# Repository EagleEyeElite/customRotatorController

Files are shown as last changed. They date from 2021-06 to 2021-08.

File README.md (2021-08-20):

# Satellite Receiver

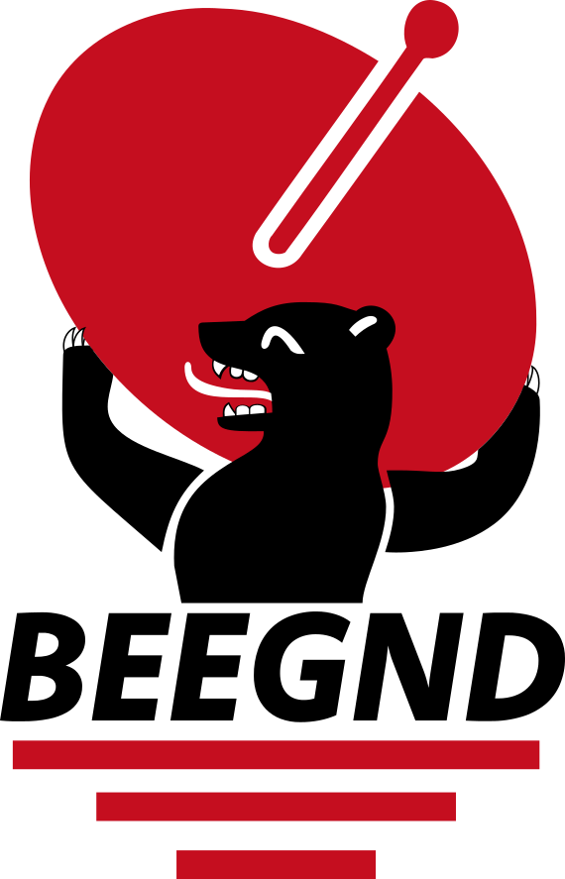
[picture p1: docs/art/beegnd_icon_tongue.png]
BEEGND IMG


Student project: custom rotor design for portable ground station. \
Members of this group:
- Conrad Klaus (code and electronics)
- Prabhpreet S. Data (mechanics, prototype)
- Nasser Mazraani (final design build)

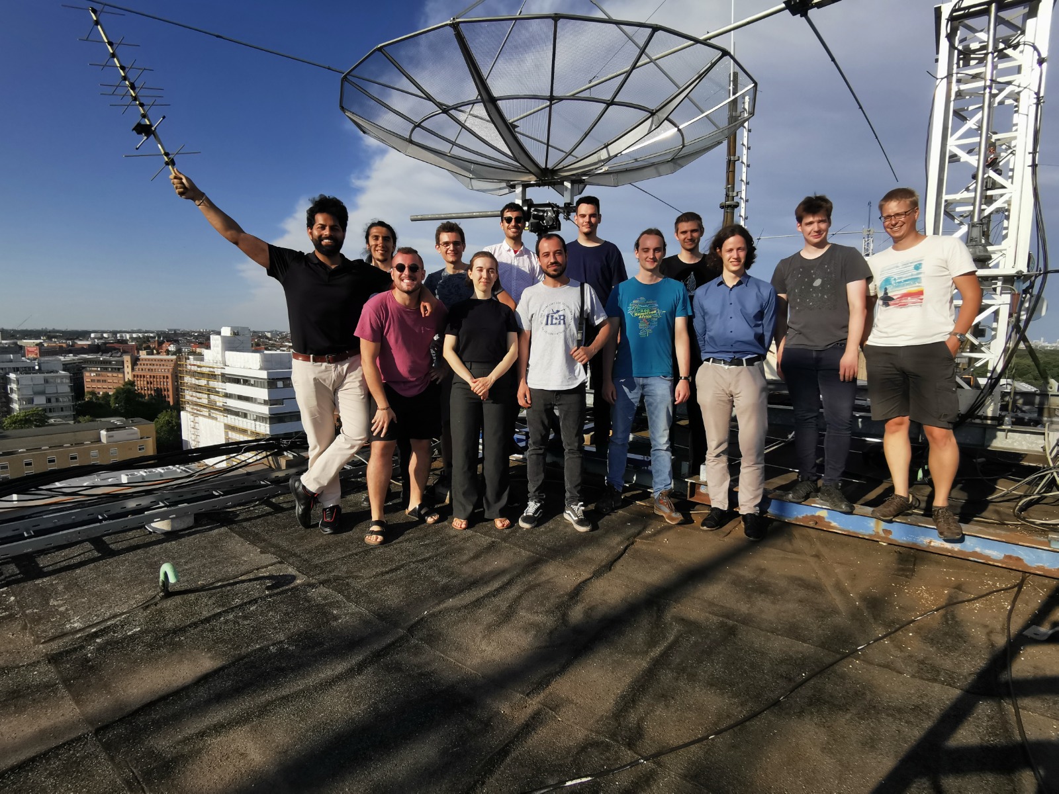
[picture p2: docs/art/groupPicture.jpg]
Satcom Group img
\
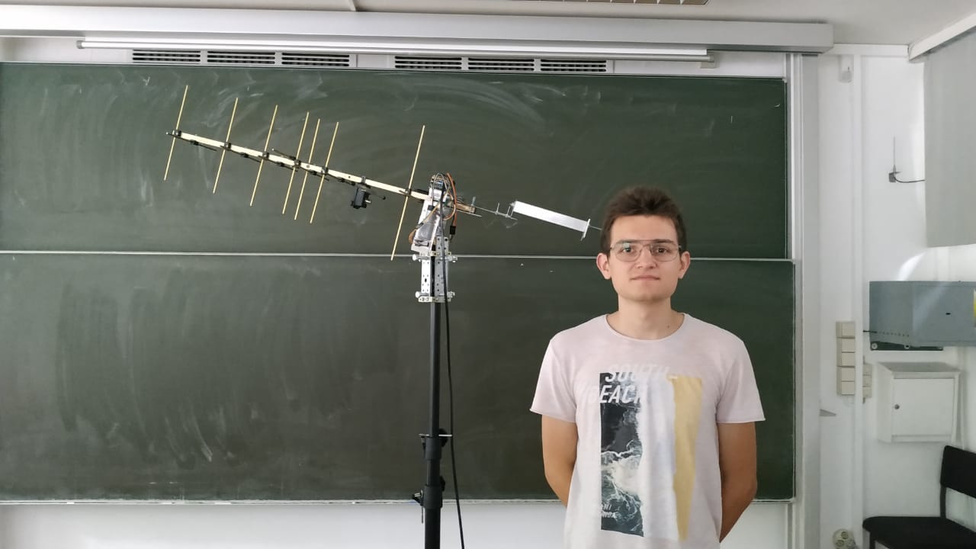
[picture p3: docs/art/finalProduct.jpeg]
Satellite Receiver img


## PCB design
The pcb is designed as a raspberry pi hat to drive the motors and sensors.\
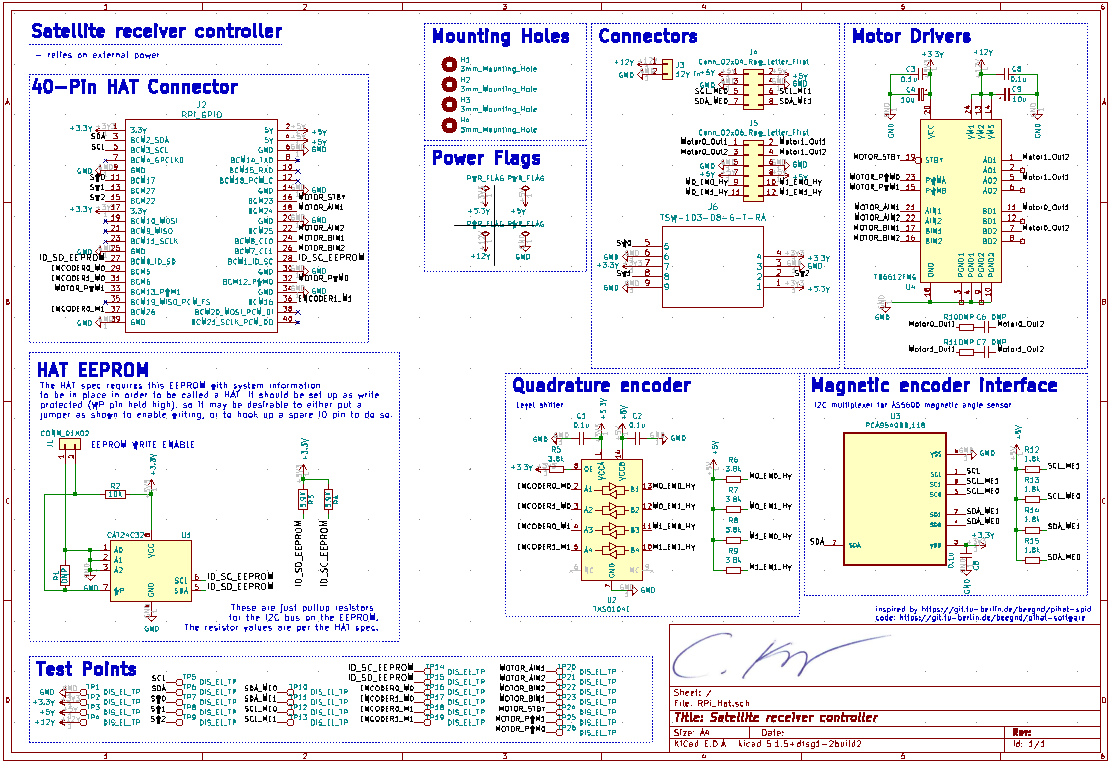
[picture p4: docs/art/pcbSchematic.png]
Pcb Schematic
\
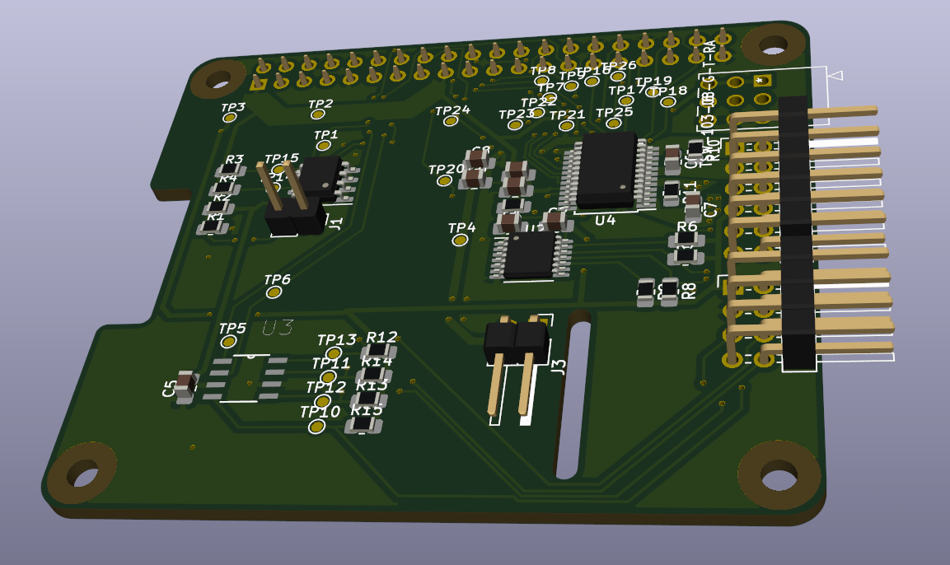
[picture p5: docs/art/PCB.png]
Pcb Image


## Code
Main features:
- Rotctl
- Multithreading
- Sensors: magnetic encoder, quadrature
encoder, switches
- Separate driver modules: h-bridge, i2c
multiplexer etc.
- Position monitoring

For further information: ./src/README.md or ./documentation

Code structure: \
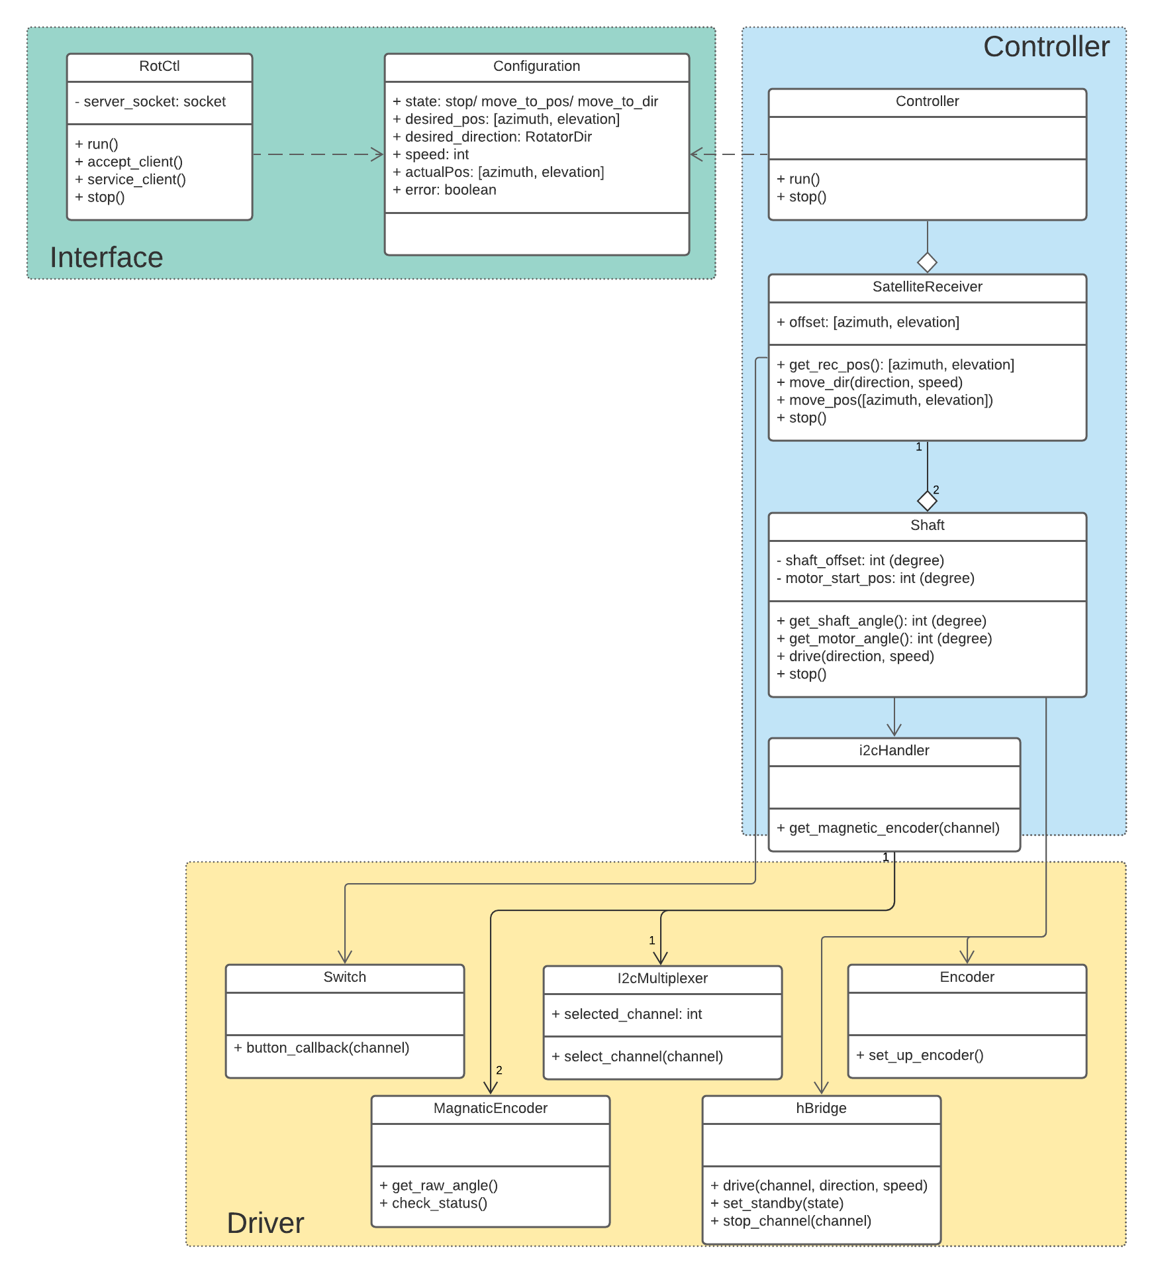
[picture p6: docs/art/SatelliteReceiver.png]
Code structure


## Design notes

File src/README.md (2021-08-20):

# Satellite receiver
Example raspberry pi ip: 10.42.0.101

## Connect to RotCtl API
The satellite receiver is controlled by rotctl. \
Run in terminal to connect to service:
```
rotctl -m 2 -r 10.42.0.101:4533
```

## Start RotCtl service
Start RotCtl service and set up virtual python environment (if needed).
```
python3 -m venv ./venv      # create venv (optional)
source ./venv/bin/activate
python3 -m pip install -r requirements.txt   # install dependencies (optional)
cd satelliteReceiver/src/
./main.py     # start controller
deactivate
```

You may need to enable I2C once in the
[raspberry pi config](https://www.raspberrypi-spy.co.uk/2014/11/enabling-the-i2c-interface-on-the-raspberry-pi).

## Connect to the pi manually
Connect ethernet adapter and raspberry first. \
Run in terminal:
```
$ ifconfig  # copy inet: (usually 10.42.0.1)
$ nmap -n -sP 10.42.0.255/24  # scans the network
```
Copy the ip address from the pi to connect to it via ssh.

Access pi via explorer:
```
nfs://10.42.0.101/home/pi/satcom/customRotatorController
```

## Headless raspberry pi setup
- pc client fstab example (static ip):
  ```  
  10.42.0.101:/home/pi/satcom/customRotatorController /home/conrad/Documents/piGitMnt nfs defaults 0 0
  ```
- [ssh](https://linuxize.com/post/how-to-enable-ssh-on-raspberry-pi/)
- [wifi](https://www.raspberrypi.org/documentation/configuration/wireless/headless.md)
- laptop ethernet setup:
    - [static ip](https://www.circuitbasics.com/how-to-connect-to-a-raspberry-pi-directly-with-an-ethernet-cable/)
    - [dynamic ip](https://stackoverflow.com/questions/16040128/hook-up-raspberry-pi-via-ethernet-to-laptop-without-router)
- [nfs workflow](https://pimylifeup.com/raspberry-pi-nfs/)

## Used hardware
- [Power over ethernet hat](https://www.amazon.de/dp/B091YZ2QSM)
- [Motor 10RPM](https://www.banggood.com/Machifit-JGY-370-DC-12V-103090150RPM-Motor-Reduction-Gear-Turbine-Worm-Self-locking-Encoder-Signal-Feedback-Motor-p-1504101.html)
- [Magnetic encoder](https://www.amazon.de/dp/B08K2Q96V1/)
  
## Sources
- [KiCad pi Hat template](https://github.com/xesscorp/RPi_Hat_Template)

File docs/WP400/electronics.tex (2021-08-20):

\subsection{Electronics}
The custom rotator is controlled by a Raspberry Pi, extended by a custom Raspberry Pi hat. The hat provides functionality to read the safety switches, communicate to two independent magnetic encoders, drive both motors, and monitor the motors speed with a quadrature encoder. The Hat also features an EEPROM, which is specified by the Raspberry Pi foundation, to call it an 'official' pi hat. The pi and both motors are powered through an of the shelf power over Ethernet (POE) adapter.

\subsubsection{choice of electronics}
We had a working prototype within the first couple of weeks, which enabled us to test lots of features early on. In the beginning, we needed three cables to power the Raspberry Pi, the motors, as well as to provide a data cable for communication. The power over Ethernet adapter allowed us to only have one cable and simplify the design.
To move away from our original breadboard design connected to some of the shelves components, we also designed our Raspberry Pi hat.

\subsubsection{how to connect, pinout}

The motors we used had a standard female header with a 2.54 mm pitch. We decided to stick with these connectors and used a standard female header for all connections. These female headers can be plugged into the matching male header on the PCB. All Connectors match the same side as the USB/ Ethernet etc. connections on the Raspberry Pi. That's to make the overall cable management simpler and cleaner.
The connectors are stacked on top. The board can drive two motors. One motor can be plugged in to the upper row, and the other on the lower row. The three switches are stacked on each other in the same way.

\begin{figure}[H]
	\centering
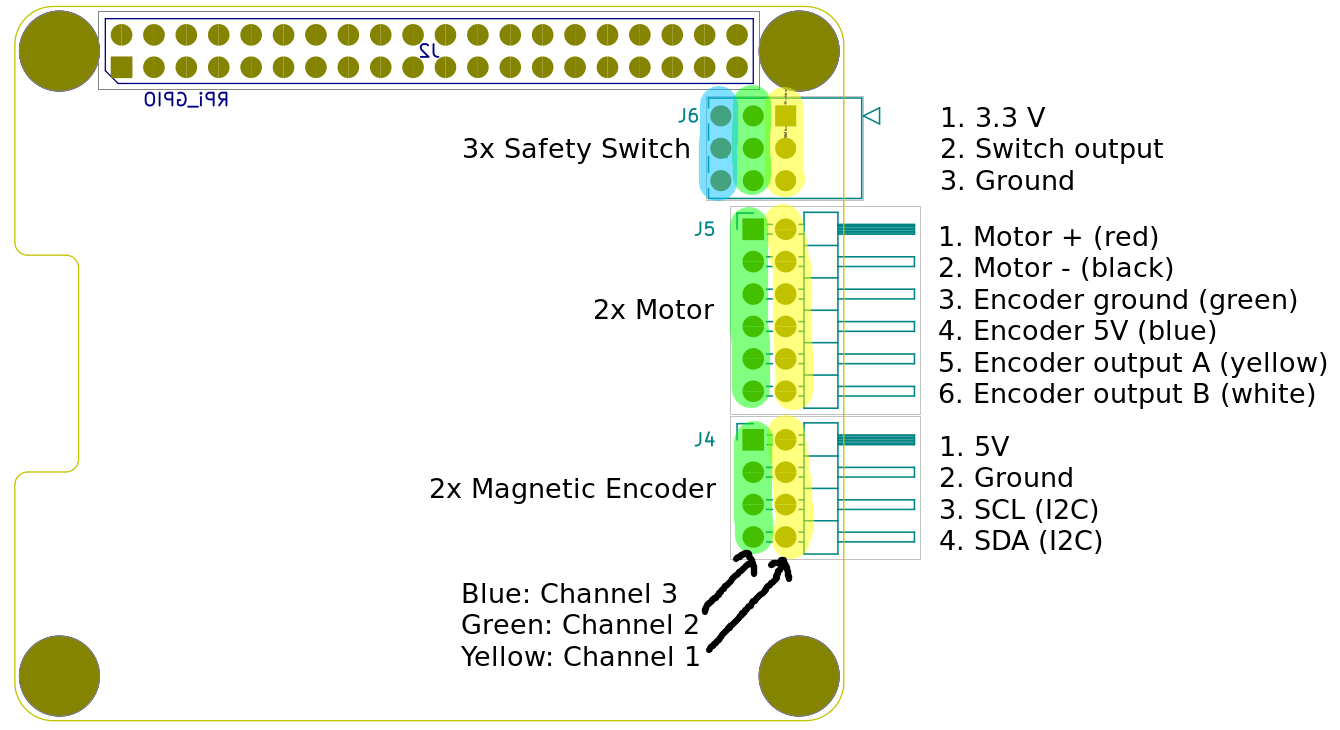
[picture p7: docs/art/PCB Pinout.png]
	
	\caption{Raspberry Pi hat pinout}
\end{figure}

\subsubsection{Electronic Design}

The Raspberry Pi controls all components on the pi hat. The h-bridge, that drives the Motors, is powered externally with a 12V power source from the power over Ethernet hat. The encoder from the motors are connected through a level shifter to the Raspberry Pi. The Switches, on the other hand, are connected to the pi directly. The magnetic encoder both use the same i2c protocol. Unfortunately, they have the same address, which can't be changed. If both encoder, are put on the same i2c bus, the pi couldn't differentiate between those two, because they use the same address. The board features therefore an i2c multiplexer, which can select on encoder at a time. The i2c multiplexer is controlled by the same i2c bus. This reduces complexity on the board, but increases complexity in the code. The following diagram shows the structure.

\begin{figure}[H]
	\centering
	
	\caption{Raspberry Pi HAT block diagram}
\end{figure}

\subsubsection{development and fabrication}

We used KiCad to design the PCB. To solder the SMD components (IC's, resistors, capacitors etc.) of the PCB, we used a soldering a reflow oven. The remaining THT components (pin headers etc.) were soldered manually. The schematic, the final pcb, as well as the manufactureing process in the reflow oven are listed in the appendix.

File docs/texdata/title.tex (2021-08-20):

%%%%%%%%%%%%%%%%%%%%%%%%%%%%%%%%%%%%%%%%%%%%%%%%%%%%%%%%%%%%%%%%%%%%%%%%%%%%%%%
%
% Titelseiten
%
%%%%%%%%%%%%%%%%%%%%%%%%%%%%%%%%%%%%%%%%%%%%%%%%%%%%%%%%%%%%%%%%%%%%%%%%%%%%%%%

\belowpdfbookmark{Title}{titlepage}

\begin{titlepage}
  \begin{tikzpicture}[
  remember picture,
  overlay
  ]
  \node [anchor = north west] at ([xshift = +10mm, yshift = -10mm]current page.north west) {
    
  };
  \end{tikzpicture}
  \begin{tikzpicture}[
  remember picture,
  overlay
  ]
  \node [anchor = north ] at ([xshift = +7 mm, yshift = -10mm]current page.north) {
    
  };
  \end{tikzpicture}
  \begin{center}
    \hspace{0pt}\vfill

    %\large Space Interdisciplinary Engineering in Radio and Robotic Applications \\ \hspace{0pt}

    \huge\textbf{Official Documentation} \\ \vspace{20pt}

    \large{Berlin Experimental and Educational Ground Station}

    \vfill

    \normalfont\normalsize Document: \nr \\
    Version: \ver\\
    Date: \dat

    \vfill

    %\includegraphics[height=\hh]{../../global_references/tuBerlinLogoRot}
    %\includegraphics[height=\hh]{../../global_references/tuBerlinLogoSchwarz}

    \normalfont\normalsize \hspace{0pt}\\
    Technische Universit\"at Berlin\\
    Department of Aeronautics and Astronautics\\
    Chair of Space Technology\\
    Office F 6\\
    Marchstraße 12--14\\
    10587 Berlin

    Tel.: 030 / 314-21305\\
    Fax: 030 / 314-21306
  \end{center}
\end{titlepage}

%%%%%%%%%%%%%%%%%%%%%%%%%%%%%%%%%%%%%%%%%%%%%%%%%%%%%%%%%%%%%%%%%%%%%%%%%%%%%%%

\begin{titlepage}
  \begin{center}
    \textbf{\huge{Technical Note}\\\hspace{0pt}}
    %\textbf{\large{This is an mple headline}\\\hspace{0pt}}
    
    \ \\
    \ \\
    \textbf{Version History\\\hspace{0pt}}
    
    \begin{tabular*}{\textwidth}
      {%
        @{}p{0.1\textwidth}
        p{0.15\textwidth}
        p{0.35\textwidth}
        p{0.3\textwidth}@{}
      }
      \toprule
      Version & Date & Changes & Processor \\
      \midrule
      0.1 & 2021-07-05 & Document creation  & Alexis Cabana-Loriaux \\
      \bottomrule
    \end{tabular*}%
    
    \vfill
    
    \thispagestyle{TUB}
    
    \pagebreak

  \vfill

     \end{center}%
  \thispagestyle{TUB}%
\end{titlepage}

%%%%%%%%%%%%%%%%%%%%%%%%%%%%%%%%%%%%%%%%%%%%%%%%%%%%%%%%%%%%%%%%%%%%%%%%%%%%%%%

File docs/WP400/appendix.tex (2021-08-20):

\section{PCB schematic and manufacturing process}

\begin{figure}[H]
	\centering
	
	\caption{Schematic of Raspberry Pi hat}
\end{figure}

\begin{figure}[H]
	\centering
	
	\caption{PCB of Raspberry Pi hat}
\end{figure}

\begin{figure}[H]
	\centering
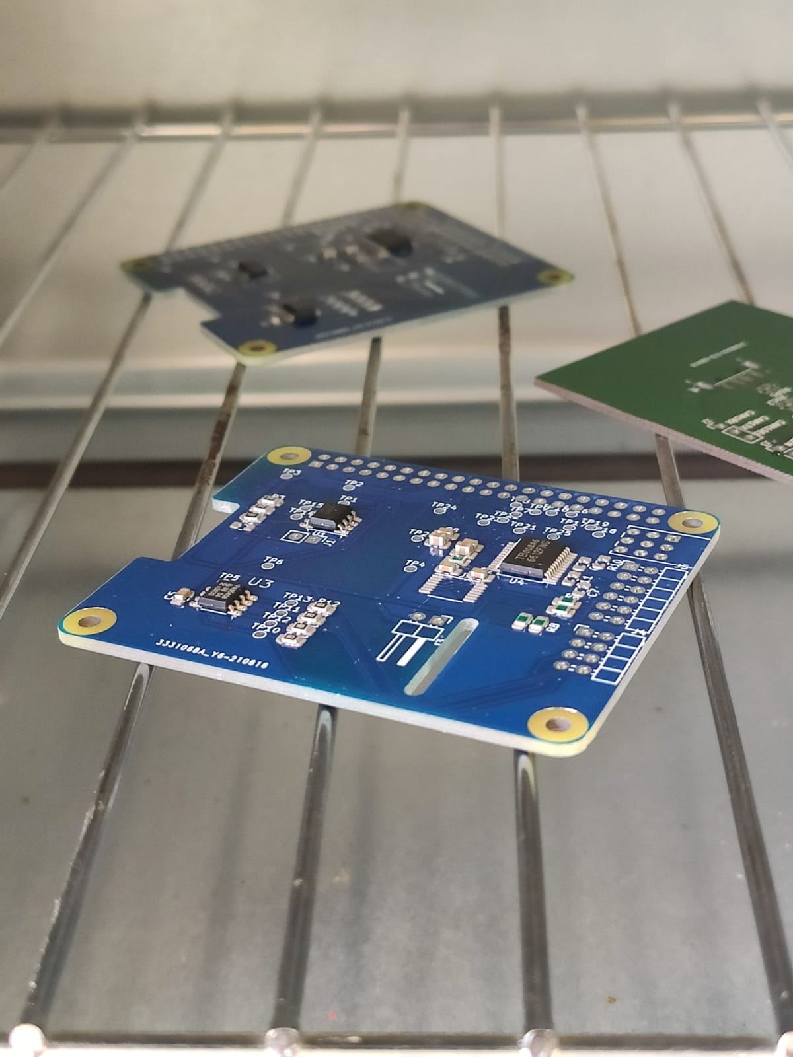
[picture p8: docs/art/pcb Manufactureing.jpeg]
	
	\caption{Raspberry Pi hat manufacturing in the reflow oven}
\end{figure}

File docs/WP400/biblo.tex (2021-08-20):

\vspace{0.5cm}

[1] https://www.sdp-si.com/D265/PDF/D265T003.pdf

[2] https://www.k-m.de/en/kmPdf/datasheet/ordernumber/21105-000-55

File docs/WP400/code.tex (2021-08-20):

\subsection{Code}

\subsubsection{Quick start}
The code is executed by the Raspberry Pi. The python script needs to be started manually. For example, you could connect to the pi via ssh on the command line. If you know the IP address of the Raspberry Pi, you can log in via (default password is 'raspberry'): 

\begin{verbatim}
ssh pi@ipAdress
\end{verbatim}

If you don't know your Raspberry Pi's IP address, you can connect the raspberry's Ethernet cable directly to your pc. See this  \href{https://www.circuitbasics.com/how-to-connect-to-a-raspberry-pi-directly-with-an-ethernet-cable/}{Guide} or this 
\href{https://stackoverflow.com/questions/16040128/hook-up-raspberry-pi-via-ethernet-to-laptop-without-router}{Guide}. If you set up the Raspberry Pi for the first time, note the src/README.md in the \href{https://github.com/EagleEyeElite/satelliteReceiver}{git repository}. Once you are logged in, start the rotctl service:

\begin{verbatim}
source ./venv/bin/activate
cd satelliteReceiver/src/
./main.py     # start controller
\end{verbatim}

Connect to the started rotctl service from your pc:
\begin{verbatim} 
rotctl -m 2 -r 10.42.0.101:4533
\end{verbatim}

\subsubsection{Code structure}

The code implements the rotctl server. It's multithreaded to serve the clients requests and oversee the rotator simultaneously. The rotator uses two magnetic encoders, connected to the differential, to gain absolute position (even after power cut off). The motor's encoder are used to monitor the motor speed. Additionally, the rotor can observe three safety switches to cut off the motors to prevent the rotator damaging itself.
The code structure represents the structure of the rotator and the electronics. All IC's like the h-bridge, the i2c multiplexer etc. have their own driver modules. The rotator itself and the two shafts connected to the differential are also represented as objects. Note \ref{Code_structure} to see the full code structure:

\begin{figure}[H]
	\centering
	
	\caption{Code structure}
	\label{Code_structure}
\end{figure}

Once the python script is started, two independent threads are started. One thread handles all communication to different clients, and the other thread handles the movement of the controller. They interact through a configuration object. The rotctl sets a desired position, direction or a stop signal. It also reads out the current actual position of the rotator. The Controller on the other hand read out the desired position, direction and the stop signal and sets the actual position.

This separation allows the rotctl server to be non-blocking.

If the client requests position A and then quickly request position B, the rotator doesn't need to wait until it moved to position A to then move the position B. With this separation it can simply discard the old request and move to the new request immediately.

All values in the configuration object are always updated by only one thread. The values are also not used for further computation. Even though racing condition can occur, the code is still thread safe.

\begin{figure}[H]
	\centering
	
	\caption{Raspberry Pi HAT flow diagram}
\end{figure}

\subsubsection{Possible improvements}
The time constrains didn't allow to make any real use of the EEPROM on the pi hat. With more time, it would be possible to save a configuration on that EEPROM, to set up pi the pi automatically. The I2C bus, for example, could be enabled, as soon as the board is plugged in.

In a demonstration video, we showed the movement of the rotator. The readings of all sensors work well. Unfortunately, more testing is required on the position calculation. As of now, we still assume some bugs in the algorithm to get the current position. The safety switches are included in the code, but not yet on the actual rotator. It's effortless to stop the rotator at any given time per command over rotctl or over the ssh connection. Playing around with it doesn't introduce a huge risk. But we don't recommend putting it up somewhere and to expect, that it doesn't break itself eventually.

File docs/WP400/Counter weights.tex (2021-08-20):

\subsubsection{Counter weights}
\subsubsection*{Arm weight balancing}
After deciding on the section of the boom that would be fixed to the rotator, we proceeded to determine the required force and its location to neutralize the weight acting on the antenna arm for this pivot point. We found the center of gravity of the antenna and then commenced moving it backwards until it sits at the center of the upper plate where it is mounted. A mass of 0.8 kg was calculated to be required at 13.5 cm from the center (from center to center). This value varies slightly depending on the shape of the weight attached. Conveniently, we found some microphone boom weights with the same value and that also attach to the same diameter of the boom we have. However sometimes an adapter might be required, and this would have slight implications on the position of the counterweight as we take into account the additional mass in that location. Figures 400.11 and 400.12 show the counter weight options. 
\begin{figure}[H]
	\centering
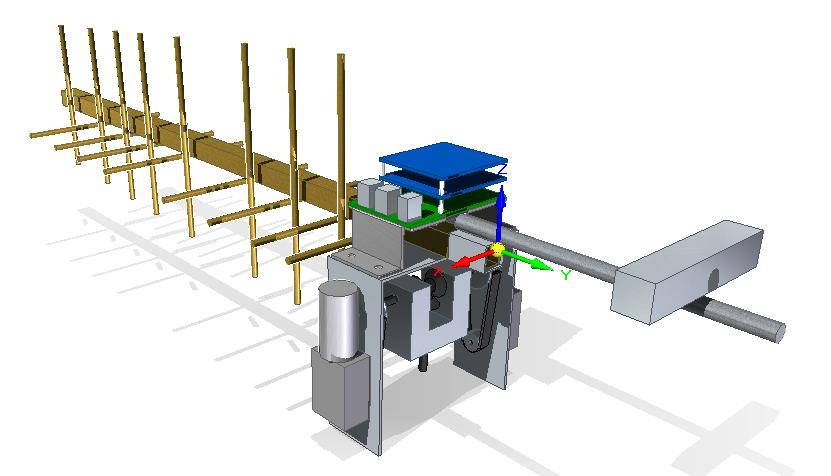
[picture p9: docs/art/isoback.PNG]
	
	\caption{Arm weight balancing}
\end{figure}

\begin{figure}[H]
	\centering
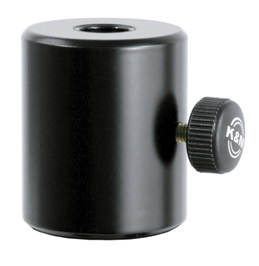
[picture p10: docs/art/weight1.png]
	
	\caption{Commercial 0.8 kg counter weight. [2]}
\end{figure}

\subsubsection*{Pitch mass shift compensation} 
Pitch mass shift counter weights are used to balance the centre of gravity in vertical axis. The final target is to balance centre of gravity at rotational axis of the rotator. This will put negligible load on motors and motors have to overcome just inertia. The considered rotator design requires balancing of centre of gravity in both horizontal and vertical axis.  To compensate real case variations, dead weights are mounted on COTS threaded rods. This helps the user to balance the centre of gravity with extreme accuracy. Figure 400.13 shows the pitch mass weights. 

\begin{figure}[H]
	\centering
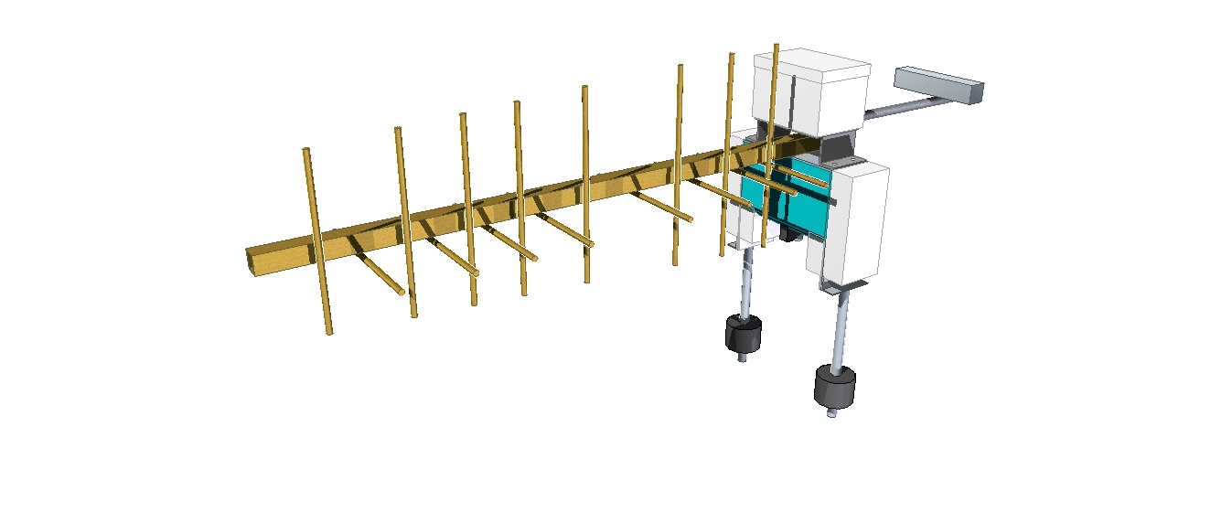
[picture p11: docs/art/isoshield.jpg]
	
	\caption{Pitch mass weights}
\end{figure}

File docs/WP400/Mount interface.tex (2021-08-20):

\subsubsection{Mount interface}
Rotator is designed to be mounted on tripod and can be deployed outdoors. To fulfil this requirement a standard mount is designed which can provide mechanical joint between differential shaft of rotator and tripod rod as shown in following figure 400.8.  
\begin{figure}[H]
	\centering
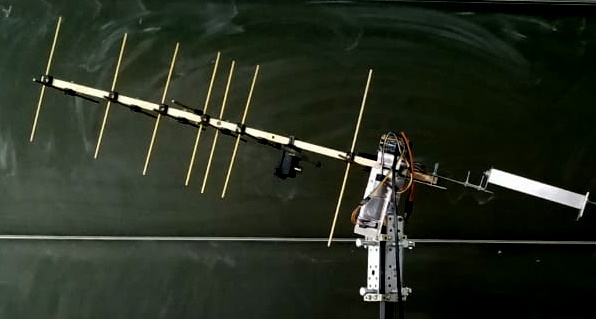
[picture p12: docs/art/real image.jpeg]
	
	\caption{Mount Prototype}
\end{figure}

\subsubsection*{Mount interface design methodology}
Design of mount is inspired from lathe chuck which has mechanism to hold any work-piece. In this design similar capability is achieved by providing 8 nut bolts which can hold tripod of 10 mm to 40 mm diameter. Further this design has capability to compensate levelling of rotator with respect to horizon by 10 deg. on each side. Following figure shows mount and it’s connection differential gear.   

\begin{figure}[H]
	\centering
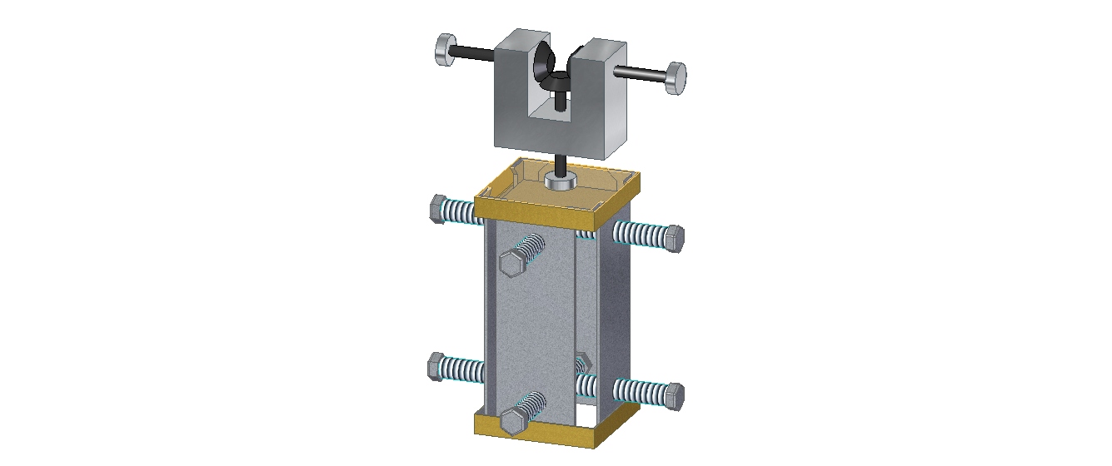
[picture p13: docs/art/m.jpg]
	
	\caption{Mount image CAD}
\end{figure}

\subsubsection*{Scope of improvements}
Other mounting options can be explored to reduce the cost and complexity of the design. These improvement can be implemented by using off the shelf technologies. One of the option is usage of sound box adaptor for mount as shown in figure 400.10.     

\begin{figure}[H]
	\centering
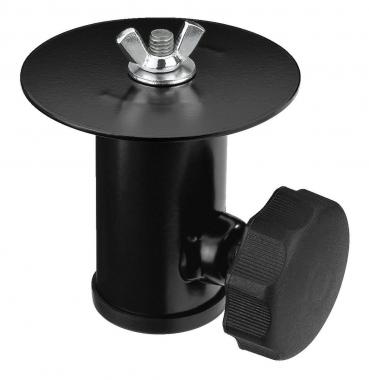
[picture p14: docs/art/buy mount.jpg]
	
	\caption{Example of off shelf technology}
\end{figure}

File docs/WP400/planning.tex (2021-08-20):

Initially the system performance requirements were defined. It should be noted however that the team could not manage to meet some of these requirements within the project timeline, specifically OR01, and ER03.
\subsection{System requirements}
\textbf{FR01}: The rotator must be able to move the antenna around the vertical and lateral axis.\\
\textbf{FR02}: The rotator should have a pointing accuracy of $2\degree$.\\
\textbf{FR03}: The rotator should be able to accelerate at $10\degree/s²$ max.\\
\textbf{FR04}: The rotator must have a directional velocity of $5\degree/s$ typical to $20\degree$ max.\\
\textbf{OR01}: The rotator must be able to automatically track satellites.\\
\textbf{ER01}: The rotator must be able to withstand temperatures between $-10\degree C$ and $+40\degree C$.\\
\textbf{ER02}: The rotator must be able to withstand wind loads up to 25 km/s.\\
\textbf{ER03}: The rotator shielding must be able to block rain capacities up to 5 cm/hr.\\
\textbf{LR01}: The rotator must be installable within 10 minutes on site.\\
\textbf{DR01}: The rotator mounting shall be adaptable to standard 35 mm tripod masts.\\
\\
FR: Functional Requirements, OR: Operational Requirements, LR: Logistics Support Requirements, ER: Environmental Requirements, DR: Design Requirement.

\subsection{Work breakdown structure}
The flow of work is subdivided into three main technical branches and the final documentation.
\begin{figure}[H]
	\centering
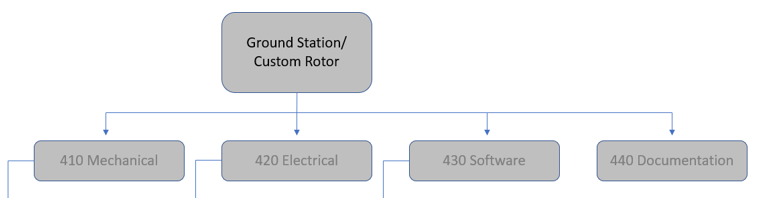
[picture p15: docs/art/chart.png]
	
	\caption{Excerpt from WP-400 work breakdown chart.}
\end{figure}

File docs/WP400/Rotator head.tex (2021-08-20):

\subsubsection{Rotator head}
\subsubsection*{Concept Overview}
The basic concept of the rotation mechanism relies on an assortment of three bevel gears set up in a T-configuration. The central shaft would be mounted vertically to the main mount and the other collinear shafts each attached to an individual JGY 370 12 V DC motor. The action of these motors against the gear assembly would allow for rotation in both the azimuth and elevation directions. This is achieved through attaching an inverted U-shaped aluminum bracket that forms the main fixture structure of the whole rotator. The sides of the bracket are each attached to one of the driven shafts and their relevant motors, while the top face serves as the mounting location of the antenna and printed circuit boards including the Raspberry Pie 4.\\
When the opposing motors rotate in the same direction i.e. both clockwise, the gears are able to transform this into movement in the azimuth direction. This is due to the reaction against the central fixed gear.\\
However, when ordered to rotate in opposing directions this is translated into gears rotating in the same direction against the central gear. This of course will not be physically possible and hence the gear point is fixed, and the rotation motion is transferred to the motors themselves around the axis and by that consequently moving the bracket up or down, changing the elevation sense of the antenna.

\begin{figure}[H]
	\centering
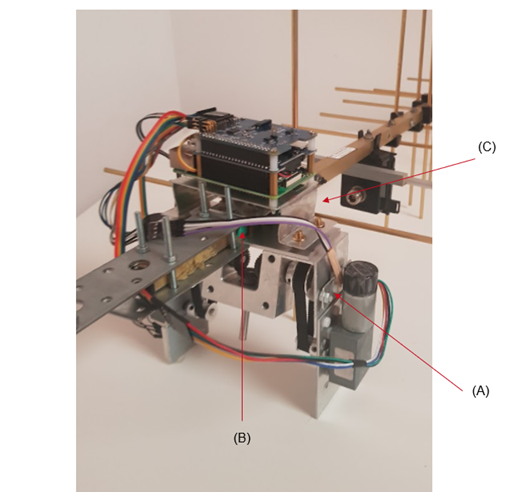
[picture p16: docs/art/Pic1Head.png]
	
	\caption{Rotator Head without shielding.}
\end{figure}

\subsubsection*{Design} 
The initial conditions to be met were the first driving parameters for the design. Namely, the required torque was first investigated. Assuming that this portable rotator would not be tested in storms, the highest of the average of wind speeds in Germany was considered, that being during January, and then rounded to get 19.5 km/h. Since we imagined using a cross Yagi antenna for this application, we took into account one face of the boom and calculated the area to be 0.15 m\^2, the directors being cylindrical and of small diameter were also estimated and found to be of negligible effect if exposed to wind drag. This put together along with the reflector and other parts did not amount to much in relation to torque requirements. The torque required was calculated to be less than 0.25 N however we decided to use this value for safety, and to allow more flexibility for use with other types or shapes of antennas. Separately the average torque of one motor was found to be around 1.3 N/m. While this was sufficient and tested on the first prototype to be adequate for controlling the rotator with a dummy weight, we later decided to double this potential by two, and this was achieved by utilizing a belt and pulley system with a ratio of 2:1.\\
The belts and pulleys in concern are those of GT2 pulleys, and 9mm timing belts. The same class of belts and pulleys used in most commercial 3D printers. This design decision seemed logical for two reasons, one being the need of precise movement and transmission without slippage as is the case for 3D printers, and the other being the affordability and availability characteristics of said parts. A permanent relative position and a constant speed ratio are easy to expect using this product while also being able to handle heavy loads. [1]\\
Constrained by the purchased belt length\footnote{Due to logistics the favored belt length could not be available within time and the design was iterated to fit a new belt.} and the available GT2 pulleys we could finally define the distance between the centers of the horizontal gear and motor shafts. This parameter would also aid in defining the length of the side member of the main bracket to allow for this assembly while taking into account mounting locations of other components of the system. \\
This distance mentioned earlier would be the distance required between the pulleys to fit the belt effectively and ensure efficient functionality. We determined this distance by first investigating the outer diameters of each pulley and then plugging it along with the belt length into this equation:\\
\begin{center}
    $\frac{b+ \sqrt{b^2-32(D-d)^2} }{16}=C$
\end{center}
Where $b=4L-6.28(D+d)$, D: Diameter of large pulley, d: Diameter of small pulley, and L = Length of the belt.\\
Another approach was by using the number of teeth of each pulley after determining the tooth style or pitch which is 2mm for our case.\\
\\
The other main distance to be defined for the bracket was the length. This describes the distance between the inner faces of the opposing sides. Those sides are assigned to support both horizontal axis of the gears. Considering many variables, such as dimensional, geometric, and support characteristics of available pillow block flange bearings, gear shaft length, sheet material thickness, and pulley sizes, the final length was defined at 12.3 cm. However, later this value was changed to 13.5 cm due to changes carried out to meet shortcomings in logistics again. This was still achievable by changing multiple aspects of the design to still be able and accommodate the bearings and shafts as required. 
\\
The final two and not very challenging dimensions to define were the width of the bracket and the mounting location of the driven shafts from the upper face of the bracket.
\\
Further into the build, two 6 mm tubes were threaded to fit into the motor shafts as extensions so we can manage to align the pulleys properly. Bushings were added at the end of each horizontal gear shaft right where they interface with the side bearings. These bushings were also drilled as required to allow the bearing's fasteners to go through them and hold onto the shafts. This is due to having the bearings at 8 mm diameter while the shafts are of a 6 mm diameter. These same bushing also serve to protect the magnets glued at the end of the shafts from getting too close to the metallic balls of the bearing\footnote{This is not a concern anymore, however in a previous method of attachment, for a worst case scenario if the magnet miss-aligns for any reason it would still rotate with the shaft as it doesn't get close enough for it to be pulled to one side alone.}. The latter mentioned magnets are positioned as such to allow reading the position of the shaft by two encoders, each mounted on one side of the bracket. Special mounting plates (A) were designed, cut, and drilled to situate those encoders at the right proximity from the magnets. According to our tests a distance beyond 5 mm was sufficient to lose a proper reading and hence we ultimately managed to install them within a clearance of 1 mm for best reading. Spacers were added between the motors and bracket faces to distance the motor ends from the encoders, while both isolating a chance of interference due to the rotating magnet of the motor's encoders and also allowing easy installation and removal of the encoders in case of inspection or issue without having to uninstall the motors and other components of the assembly first.

\subsubsection*{Material Selection}
The antenna at hand weighs no more than 0.5 kg. When balanced in its mounting location on the bracket, the only load of concern is that applying directly downwards on the bridge. A secondary concern would be the torsional load on the same plate when the rotator moves at its lateral axis. Several design solutions were planned, however using the final procurement, it was found that this issue is easily treated by using an aluminum plate thickness of 3 mm. It must be noted that this was not possible in the initial design because a thickness more than 2 mm for the sides would result in other considerations because we are constrained by certain dimensions of the bearing flanges which would lead to disruption of other parameters as well. However, using the modular approach, we were able to simply use an aluminum plate of a larger thickness for the top section.\\
\\
A FEM analysis shows how the current design handles the load of the antenna.\\
\\
(Include simulation here.) Figure.

\subsubsection*{Antenna Strainer}
The design for the antenna mount varied. Two similar concepts were finally tracked, one would be using a bent aluminum sheet, and another is 3D printed.\\
\\
Note: The metal sheet work required a wait time of two weeks in the workshop due to a busy schedule, and the 3D printed part was never delivered as technical problems with the printer were reported during the job.
\begin{figure}[H]
\centering
\begin{subfigure}{.5\textwidth}
  \centering
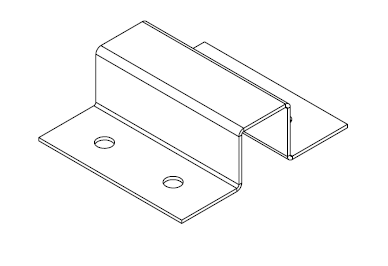
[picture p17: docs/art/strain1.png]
  
  \caption{Machined part.}
  \label{fig:sub1}
\end{subfigure}%
\begin{subfigure}{.5\textwidth}
  \centering
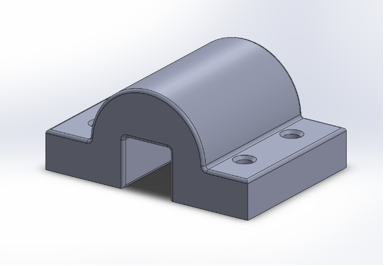
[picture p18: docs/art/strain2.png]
  
  \caption{3D printed part.}
  \label{fig:sub2}
\end{subfigure}
\caption{This figure shows two of the final antenna holders.}
\label{fig:test}
\end{figure}
On the final presentation the antenna was fixed using a sandwich of aluminum plates, constrained by 3 bolts on each side, and wrapped in a rubber material (B) as an interface between the antenna boom and the bolts and plates to increase traction considerably and avoid any chance of slippage during operation (Figure 2).

\subsubsection*{PCB Mounting}
A custom-made bridge (C) was drawn and fabricated to mount the PCB sandwich (Figure 2).

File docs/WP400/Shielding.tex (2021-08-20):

\subsection{Electronics}
The custom rotator is controlled by a raspberry pi, extended by a custom raspberry pi hat. The hat provides functionallity to read the safty swiches, communicate to two independet magnetic encoder, drive both motors, as well as monitor the motors speed with a quadrature encoder. The Hat also features a EEPROM, which is specified by the raspberry pi foundation, to call it an 'offical' pi hat. The pi and both motors are powered through an of the shelf power over ethernet (poe) adapter.

\subsubsection{choice of electronics}
We had a working prototype within the first couple of weeks, which enabled us to test lots of feature early on. In the beginning, we needed three cables to power the raspberry pi, the motors, as well as to provide a data cable for communication. The power over ethernet adapter allowed us to only have one cable and simplify the design.
To move away from our orignal breadboard design connected to some of the shelfs components, we also designed our own raspberry pi hat.

\subsubsection{how to connect, pinout}
\begin{figure}[h]
	\centering
	
	\caption{Raspberry pi hat pinout}
\end{figure}

\subsubsection{Electronic Design}

\begin{figure}[h]
	\centering
	
	\caption{Raspberry pi HAT blockdiagramm}
\end{figure}

\begin{figure}[h]
	\centering
	
	\caption{Schematic of Raspberry Pi hat}
\end{figure}

\begin{figure}[h]
	\centering
	
	\caption{PCB of Raspberry Pi hat}
\end{figure}

\begin{figure}[h]
	\centering
	
	\caption{Raspberry pi manufacturing}
\end{figure}

\subsubsection{fabrication and rework}

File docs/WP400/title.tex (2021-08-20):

%%%%%%%%%%%%%%%%%%%%%%%%%%%%%%%%%%%%%%%%%%%%%%%%%%%%%%%%%%%%%%%%%%%%%%%%%%%%%%%
%
% Titelseiten
%
%%%%%%%%%%%%%%%%%%%%%%%%%%%%%%%%%%%%%%%%%%%%%%%%%%%%%%%%%%%%%%%%%%%%%%%%%%%%%%%

\belowpdfbookmark{Title}{titlepage}

\begin{titlepage}
  \begin{tikzpicture}[
  remember picture,
  overlay
  ]
  \node [anchor = north west] at ([xshift = +10mm, yshift = -10mm]current page.north west) {
    
  };
  \end{tikzpicture}
  \begin{tikzpicture}[
  remember picture,
  overlay
  ]
  \node [anchor = north ] at ([xshift = +7 mm, yshift = -10mm]current page.north) {
    
  };
  \end{tikzpicture}
  \begin{center}
    \hspace{0pt}\vfill

    %\large Space Interdisciplinary Engineering in Radio and Robotic Applications \\ \hspace{0pt}

    \huge\textbf{Official Documentation} \\ \vspace{20pt}

    \large{Berlin Experimental and Educational Ground Station}

    \vfill

    \normalfont\normalsize Document: \nr \\
    Version: \ver\\
    Date: \dat

    \vfill

    %\includegraphics[height=\hh]{../../global_references/tuBerlinLogoRot}
    %\includegraphics[height=\hh]{../../global_references/tuBerlinLogoSchwarz}

    \normalfont\normalsize \hspace{0pt}\\
    Technische Universit\"at Berlin\\
    Department of Aeronautics and Astronautics\\
    Chair of Space Technology\\
    Office F 6\\
    Marchstraße 12--14\\
    10587 Berlin

    Tel.: 030 / 314-21305\\
    Fax: 030 / 314-21306
  \end{center}
\end{titlepage}

%%%%%%%%%%%%%%%%%%%%%%%%%%%%%%%%%%%%%%%%%%%%%%%%%%%%%%%%%%%%%%%%%%%%%%%%%%%%%%%

\begin{titlepage}
  \begin{center}
    \textbf{\huge{Technical Note}\\\hspace{0pt}}
    %\textbf{\large{This is an mple headline}\\\hspace{0pt}}
    
    \ \\
    \ \\
    \textbf{Version History\\\hspace{0pt}}
    
    \begin{tabular*}{\textwidth}
      {%
        @{}p{0.1\textwidth}
        p{0.15\textwidth}
        p{0.35\textwidth}
        p{0.3\textwidth}@{}
      }
      \toprule
      Version & Date & Changes & Processor \\
      \midrule
      0.1 & 2021-07-05 & Document creation  & Alexis Cabana-Loriaux \\
      \bottomrule
    \end{tabular*}%
    \vspace{1cm}
    \begin{tabular*}{\textwidth}
      {%
        @{}p{0.1\textwidth}
        p{0.15\textwidth}
        p{0.35\textwidth}
        p{0.3\textwidth}@{}
      }
      \toprule
      Version & Date & Sections & Author \\
      \midrule
      0.1 & 2021-08-13 & 1/2/3.1.1/3.1.4  & Nasser Mazraani \\
      \midrule
      0.1 & 2021-08-13 & 3.1.2/3.1.3/3.1.4  & Prabhpreet S. Data \\
       \midrule
      0.1 & 2021-08-13 & 3.2/3.3  & Conrad Klaus \\
      \bottomrule
    \end{tabular*}%
    
    \vfill
    
    \thispagestyle{TUB}
    
    \pagebreak

  \vfill

     \end{center}%
  \thispagestyle{TUB}%
\end{titlepage}

%%%%%%%%%%%%%%%%%%%%%%%%%%%%%%%%%%%%%%%%%%%%%%%%%%%%%%%%%%%%%%%%%%%%%%%%%%%%%%%

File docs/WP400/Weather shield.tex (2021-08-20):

\subsubsection{Weather shielding}
The custom rotator is designed to operate in outdoor environment for long duration. To avoid damage from sun light exposure and humidity, a dedicated shielding is designed for mechanical and electronics parts. The architecture of shielding is based on consideration that shielding should not hinder the mechanical movements of any part. 
\subsubsection*{Weather shielding design methodology}
The design of shielding is optimised to provide protection to the critical parts. Materials, manufacturing process and parts are from off shelf technologies and easy to manufacture. Manufacturing materials are aluminium sheet and 3D printed abs plastic. Following figure shows various components of shielding marked in green and white colour.     
\begin{figure}[H]
	\centering
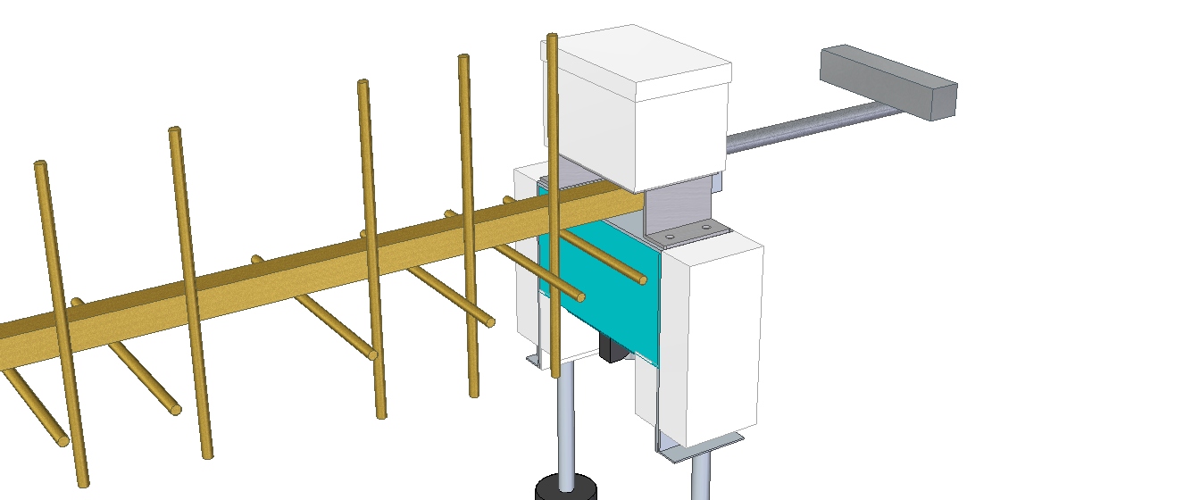
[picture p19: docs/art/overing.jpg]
	
	\caption{Rotator with Shielding}
\end{figure}

The differential shielding (green color) is responsible to provide free movement to the rotator. The design is inspired from the military vehicle design. In this approach, a grove is provided for movement of shaft and this whole structure is covered with a flexible sheet (black in colour) to provide movement capability and seal. 

\subsubsection*{Belt covering}
Belt covering is provided by 3D printed abs plastic structure and mounted by nuts and bolts on main frame. It provides easy access for repair and routine checks. Following image shows the design and the way it is going to cover the belt and pulley. The remaining top of the belt will be covered in differential shielding.     
\begin{figure}[H]
	\centering
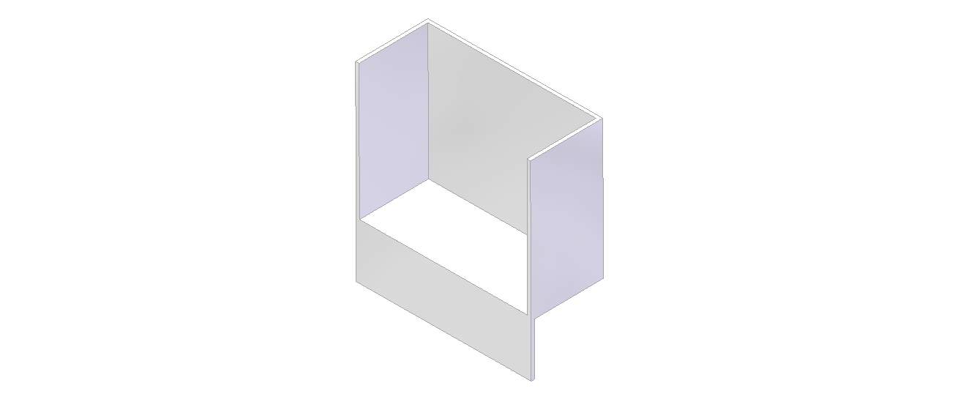
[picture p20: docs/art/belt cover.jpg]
	
	\caption{Belt Covering}
\end{figure}

\subsubsection*{Motor covering}
Motor covering is provided by 3D printed abs plastic structure and mounted by nuts and bolts on main frame. It provides easy access for repair and routine checks. Following image shows the design and the way it is going to cover motor.     
\begin{figure}[H]
	\centering
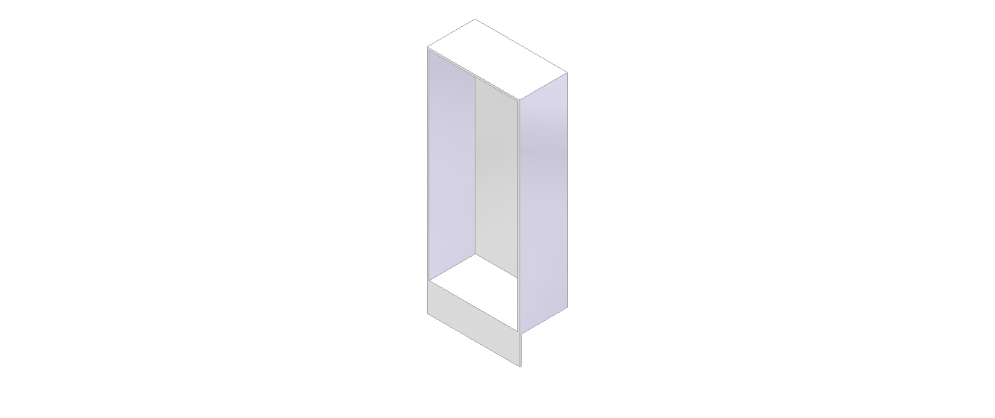
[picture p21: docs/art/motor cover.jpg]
	
	\caption{Motor Covering}
\end{figure}

\subsubsection*{Electronics Covering}
Electronics box is designed by using 3D printed abs plastic structure and mounted by nuts and bolts on main frame. It provides easy access for repair and routine checks. It is simple cuboid box with top cover lid. It is designed to provide required volume for controllers, receiver and wiring.    
\begin{figure}[H]
	\centering
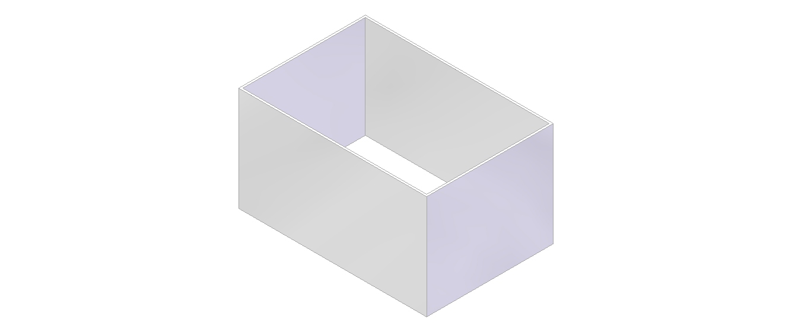
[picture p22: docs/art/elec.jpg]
	
	\caption{Electronics Covering}
\end{figure}

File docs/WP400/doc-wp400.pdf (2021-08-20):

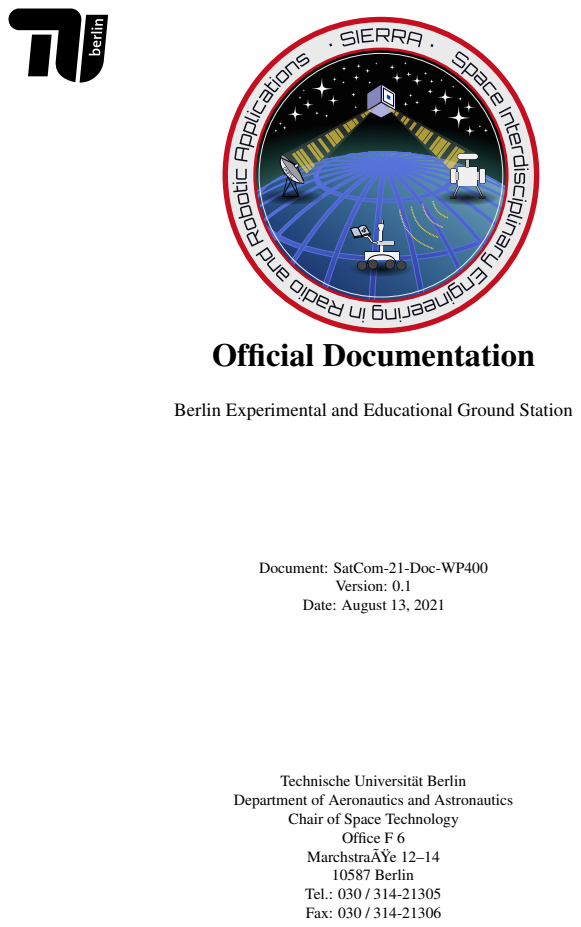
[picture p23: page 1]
Official Documentation; Version: 0.1 Date: August 13, 2021; Office F 6 MarchstraÃŸe 12–14; 10587 Berlin Tel.: 030 / 314-21305 Fax: 030 / 314-21306

Berlin Experimental and Educational Ground Station

Document: SatCom-21-Doc-WP400

Technische Universität Berlin

Department of Aeronautics and Astronautics

Chair of Space Technology

Institut für
Luft- und Raumfahrt

Fachgebiet
Raumfahrttechnik

Official Documentation - WP400 SIERRA BEEGND
Project SatCom 2021

Document:
Version:
Date:
Page:
Author:

SatCom-21-Doc-WP400
0.1
August 13, 2021
2 / 20
SatCom 2021

# Technical Note

Version History

Version | Date | Changes | Processor
0.1 | 2021-07-05 | Document creation | Alexis Cabana-Loriaux
Version | Date | Sections | Author
0.1 | 2021-08-13 | 1/2/3.1.1/3.1.4 | Nasser Mazraani
0.1 | 2021-08-13 | 3.1.2/3.1.3/3.1.4 | Prabhpreet S. Data
0.1 | 2021-08-13 | 3.2/3.3 | Conrad Klaus

©Technische Universität Berlin – Chair of Space Technology

# Contents

Table of Contents | I
400 | Portable Rotator Concept | 1
500 | Appendix | 18
Bibliography | 20

I

# List of Figures

400.1Excerpt from WP-400 work breakdown chart | | 2
400.2Rotator Head without shielding | | 3
400.3This figure shows two of the final antenna holders | | 6
400.4Rotator with Shielding | | 7
400.5Belt Covering | | 7
400.6Motor Covering | | 8
400.7Electronics Covering | | 8
400.8Mount Prototype | | 9
400.9Mount image CAD | | 9
400.10Example of off shelf technology | | 10
400.11Arm weight balancing | | 10
400.12Commercial 0.8 kg counter weight. [2] | | 11
400.13Pitch mass weights | | 11
400.14Raspberry Pi hat pinout | | 12
400.15Raspberry Pi HAT block diagram | | 13
400.16Code structure | | 15
400.17Raspberry Pi HAT flow diagram | | 16
500.1Schematic of Raspberry Pi hat | | 18
500.2PCB of Raspberry Pi hat | | 19
500.3Raspberry Pi hat manufacturing in the reflow oven | | 19

II

Luft- und Raumfahrt

Fachgebiet
Raumfahrttechnik

Official Documentation - WP400 SIERRA BEEGND
Project SatCom 2021

Version:
Date:
Page:
Author:

0.1
August 13, 2021
1 / 20
SatCom 2021

# 400 Portable Rotator Concept

## Abstract

This report demonstrates an overview of the planning process and work carried out throughout the semester by the team to design and build a new antenna rotator concept.

## 400.1 Introduction

Various rotators are available and used in controlling the attitude of different types of antennas. For this project the motivation is to develop a new concept to be used with a portable station and able to track satellites, and to achieve this it is designed to move in both azimuth and elevation directions. To meet the requirements, the rotator is characterized by being low cost and based on commercial off-the-shelf parts to compete with available models on the market.
The idea is to have a transportable and remotely controllable rotator to test the signal strength of telemetry data that is received in different locations from satellites in a low earth orbits.
This concept can be replicated by other interested individuals and is open for improvements. The sections of the report are divided into mechanical and electronic design of the product and covers its calibration and testing plan.

## 400.2 Project Planning

Initially the system performance requirements were defined. It should be noted however that the team could not manage to meet some of these requirements within the project timeline, specifically OR01, and ER03.

### 400.2.1 System requirements

FR01: The rotator must be able to move the antenna around the vertical and lateral axis. FR02: The rotator should have a pointing accuracy of 2◦
FR03: The rotator should be able to accelerate at 10◦/s
2 max.
FR04: The rotator must have a directional velocity of 5◦/s typical to 20◦ max.
OR01: The rotator must be able to automatically track satellites.
ER01: The rotator must be able to withstand temperatures between −10◦C and +40◦C. ER02: The rotator must be able to withstand wind loads up to 25 km/s.
ER03: The rotator shielding must be able to block rain capacities up to 5 cm/hr.
LR01: The rotator must be installable within 10 minutes on site.
DR01: The rotator mounting shall be adaptable to standard 35 mm tripod masts.

Luft- und Raumfahrt

Fachgebiet
Raumfahrttechnik

Official Documentation - WP400 SIERRA BEEGND
Project SatCom 2021

Version:
Date:
Page:
Author:

0.1
August 13, 2021
2 / 20
SatCom 2021

FR: Functional Requirements, OR: Operational Requirements, LR: Logistics Support Requirements, ER: Environmental Requirements, DR: Design Requirement.

### 400.2.2 Work breakdown structure

The flow of work is subdivided into three main technical branches and the final documentation.


Figure 400.1: Excerpt from WP-400 work breakdown chart.

## 400.3 Project Work

### 400.3.1 Mechancial

400.3.1.1 Rotator head

Concept Overview

The basic concept of the rotation mechanism relies on an assortment of three bevel gears set up in a T-configuration. The central shaft would be mounted vertically to the main mount and the other collinear shafts each attached to an individual JGY 370 12 V DC motor. The action of these motors against the gear assembly would allow for rotation in both the azimuth and elevation directions. This is achieved through attaching an inverted U-shaped aluminum bracket that forms the main fixture structure of the whole rotator. The sides of the bracket are each attached to one of the driven shafts and their relevant motors, while the top face serves as the mounting location of the antenna and printed circuit boards including the Raspberry Pie 4.
When the opposing motors rotate in the same direction i.e. both clockwise, the gears are able to transform this into movement in the azimuth direction. This is due to the reaction against the central fixed gear.
However, when ordered to rotate in opposing directions this is translated into gears rotating in the same direction against the central gear. This of course will not be physically possible and hence the gear point is fixed, and the rotation motion is transferred to the motors themselves around the axis and by that consequently moving the bracket up or down, changing the elevation sense of the antenna.

Luft- und Raumfahrt

Fachgebiet
Raumfahrttechnik

Official Documentation - WP400 SIERRA BEEGND
Project SatCom 2021

Version:
Date:
Page:
Author:

0.1
August 13, 2021
3 / 20
SatCom 2021


Figure 400.2: Rotator Head without shielding.

Design

The initial conditions to be met were the first driving parameters for the design. Namely, the required torque was first investigated. Assuming that this portable rotator would not be tested in storms, the highest of the average of wind speeds in Germany was considered, that being during January, and then rounded to get 19.5 km/h. Since we imagined using a cross Yagi antenna for this application, we took into account one face of the boom and calculated the area to be 0.15 m2, the directors being cylindrical and of small diameter were also estimated and found to ˆ be of negligible effect if exposed to wind drag. This put together along with the reflector and other parts did not amount to much in relation to torque requirements. The torque required was calculated to be less than 0.25 N however we decided to use this value for safety, and to allow more flexibility for use with other types or shapes of antennas. Separately the average torque of one motor was found to be around 1.3 N/m. While this was sufficient and tested on the first prototype to be adequate for controlling the rotator with a dummy weight, we later decided to double this potential by two, and this was achieved by utilizing a belt and pulley system with a

Luft- und Raumfahrt

Fachgebiet
Raumfahrttechnik

Official Documentation - WP400 SIERRA BEEGND
Project SatCom 2021

Version:
Date:
Page:
Author:

0.1
August 13, 2021
4 / 20
SatCom 2021

ratio of 2:1.
The belts and pulleys in concern are those of GT2 pulleys, and 9mm timing belts. The same class of belts and pulleys used in most commercial 3D printers. This design decision seemed logical for two reasons, one being the need of precise movement and transmission without slippage as is the case for 3D printers, and the other being the affordability and availability characteristics of said parts. A permanent relative position and a constant speed ratio are easy to expect using this product while also being able to handle heavy loads. [1]
Constrained by the purchased belt length¹
and the available GT2 pulleys we could finally define the distance between the centers of the horizontal gear and motor shafts. This parameter would also aid in defining the length of the side member of the main bracket to allow for this assembly while taking into account mounting locations of other components of the system.
This distance mentioned earlier would be the distance required between the pulleys to fit the belt effectively and ensure efficient functionality. We determined this distance by first investigating the outer diameters of each pulley and then plugging it along with the belt length into this equation:

b+

√
b

2−32(D−d)

2
16 | = C

Where b = 4L−6.28(D+d), D: Diameter of large pulley, d: Diameter of small pulley, and L = Length of the belt.
Another approach was by using the number of teeth of each pulley after determining the tooth style or pitch which is 2mm for our case.

The other main distance to be defined for the bracket was the length. This describes the distance between the inner faces of the opposing sides. Those sides are assigned to support both horizontal axis of the gears. Considering many variables, such as dimensional, geometric, and support characteristics of available pillow block flange bearings, gear shaft length, sheet material thickness, and pulley sizes, the final length was defined at 12.3 cm. However, later this value was changed to 13.5 cm due to changes carried out to meet shortcomings in logistics again. This was still achievable by changing multiple aspects of the design to still be able and accommodate the bearings and shafts as required.
The final two and not very challenging dimensions to define were the width of the bracket and the mounting location of the driven shafts from the upper face of the bracket.
Further into the build, two 6 mm tubes were threaded to fit into the motor shafts as extensions so we can manage to align the pulleys properly. Bushings were added at the end of each horizontal gear shaft right where they interface with the side bearings. These bushings were also drilled as required to allow the bearing’s fasteners to go through them and hold onto the shafts. This is due to having the bearings at 8 mm diameter while the shafts are of a 6 mm diameter. These same bushing also serve to protect the magnets glued at the end of the shafts from getting too close

1Due to logistics the favored belt length could not be available within time and the design was iterated to fit a new belt.

Luft- und Raumfahrt

Fachgebiet
Raumfahrttechnik

Official Documentation - WP400 SIERRA BEEGND
Project SatCom 2021

Version:
Date:
Page:
Author:

0.1
August 13, 2021
5 / 20
SatCom 2021

to the metallic balls of the bearing²
. The latter mentioned magnets are positioned as such to allow reading the position of the shaft by two encoders, each mounted on one side of the bracket. Special mounting plates (A) were designed, cut, and drilled to situate those encoders at the right proximity from the magnets. According to our tests a distance beyond 5 mm was sufficient to lose a proper reading and hence we ultimately managed to install them within a clearance of 1 mm for best reading. Spacers were added between the motors and bracket faces to distance the motor ends from the encoders, while both isolating a chance of interference due to the rotating magnet of the motor’s encoders and also allowing easy installation and removal of the encoders in case of inspection or issue without having to uninstall the motors and other components of the assembly first.

Material Selection

The antenna at hand weighs no more than 0.5 kg. When balanced in its mounting location on the bracket, the only load of concern is that applying directly downwards on the bridge. A secondary concern would be the torsional load on the same plate when the rotator moves at its lateral axis. Several design solutions were planned, however using the final procurement, it was found that this issue is easily treated by using an aluminum plate thickness of 3 mm. It must be noted that this was not possible in the initial design because a thickness more than 2 mm for the sides would result in other considerations because we are constrained by certain dimensions of the bearing flanges which would lead to disruption of other parameters as well. However, using the modular approach, we were able to simply use an aluminum plate of a larger thickness for the top section.

A FEM analysis shows how the current design handles the load of the antenna.

(Include simulation here.) Figure.

Antenna Strainer

The design for the antenna mount varied. Two similar concepts were finally tracked, one would be using a bent aluminum sheet, and another is 3D printed.

Note: The metal sheet work required a wait time of two weeks in the workshop due to a busy schedule, and the 3D printed part was never delivered as technical problems with the printer were reported during the job.

2This is not a concern anymore, however in a previous method of attachment, for a worst case scenario if the magnet miss-aligns for any reason it would still rotate with the shaft as it doesn’t get close enough for it to be pulled to one side alone.

Luft- und Raumfahrt

Fachgebiet
Raumfahrttechnik

Official Documentation - WP400 SIERRA BEEGND
Project SatCom 2021

Version:
Date:
Page:
Author:

0.1
August 13, 2021
6 / 20
SatCom 2021


(a) Machined part. | (b) 3D printed part.

Figure 400.3: This figure shows two of the final antenna holders.

On the final presentation the antenna was fixed using a sandwich of aluminum plates, constrained by 3 bolts on each side, and wrapped in a rubber material (B) as an interface between the antenna boom and the bolts and plates to increase traction considerably and avoid any chance of slippage during operation (Figure 2).

PCB Mounting

A custom-made bridge (C) was drawn and fabricated to mount the PCB sandwich (Figure 2).

400.3.1.2 Weather shielding

The custom rotator is designed to operate in outdoor environment for long duration. To avoid damage from sun light exposure and humidity, a dedicated shielding is designed for mechanical and electronics parts. The architecture of shielding is based on consideration that shielding should not hinder the mechanical movements of any part.

Weather shielding design methodology

The design of shielding is optimised to provide protection to the critical parts. Materials, manufacturing process and parts are from off shelf technologies and easy to manufacture. Manufacturing materials are aluminium sheet and 3D printed abs plastic. Following figure shows various components of shielding marked in green and white colour.

Luft- und Raumfahrt

Fachgebiet
Raumfahrttechnik

Official Documentation - WP400 SIERRA BEEGND
Project SatCom 2021

Version:
Date:
Page:
Author:

0.1
August 13, 2021
7 / 20
SatCom 2021


Figure 400.4: Rotator with Shielding

The differential shielding (green color) is responsible to provide free movement to the rotator. The design is inspired from the military vehicle design. In this approach, a grove is provided for movement of shaft and this whole structure is covered with a flexible sheet (black in colour) to provide movement capability and seal.

Belt covering

Belt covering is provided by 3D printed abs plastic structure and mounted by nuts and bolts on main frame. It provides easy access for repair and routine checks. Following image shows the design and the way it is going to cover the belt and pulley. The remaining top of the belt will be covered in differential shielding.


Figure 400.5: Belt Covering

Luft- und Raumfahrt

Fachgebiet
Raumfahrttechnik

Official Documentation - WP400 SIERRA BEEGND
Project SatCom 2021

Version:
Date:
Page:
Author:

0.1
August 13, 2021
8 / 20
SatCom 2021

Motor covering

Motor covering is provided by 3D printed abs plastic structure and mounted by nuts and bolts on main frame. It provides easy access for repair and routine checks. Following image shows the design and the way it is going to cover motor.


Figure 400.6: Motor Covering

Electronics Covering

Electronics box is designed by using 3D printed abs plastic structure and mounted by nuts and bolts on main frame. It provides easy access for repair and routine checks. It is simple cuboid box with top cover lid. It is designed to provide required volume for controllers, receiver and wiring.


Figure 400.7: Electronics Covering

400.3.1.3 Mount interface

Rotator is designed to be mounted on tripod and can be deployed outdoors. To fulfil this requirement a standard mount is designed which can provide mechanical joint between differential shaft of rotator and tripod rod as shown in following figure 400.8.

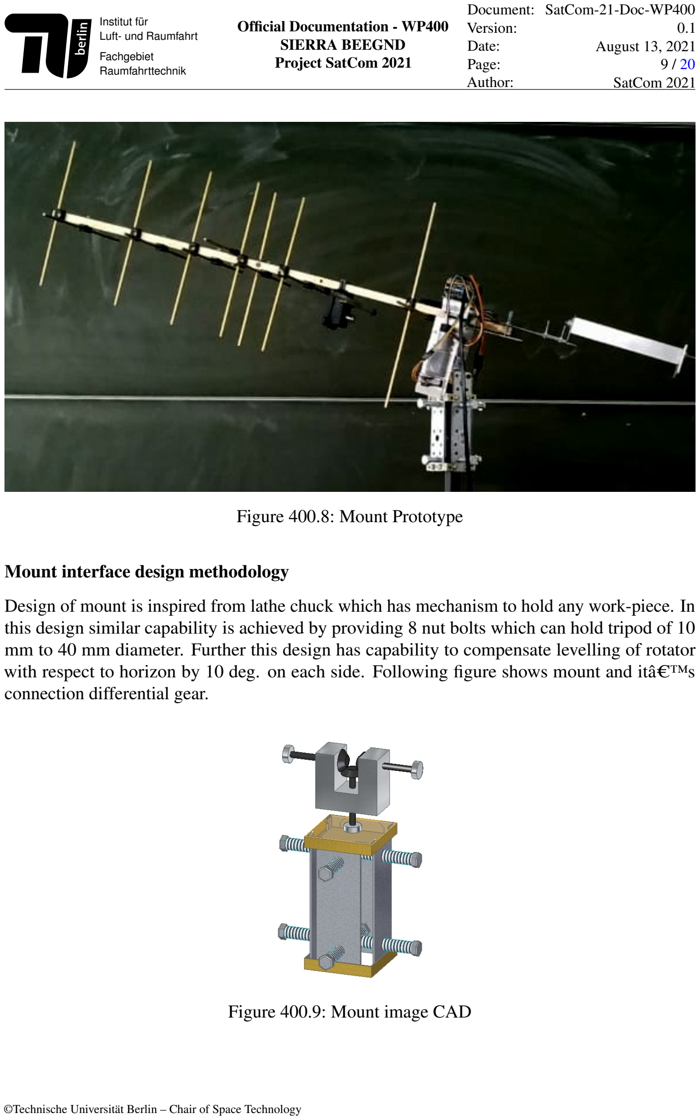
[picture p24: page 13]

Luft- und Raumfahrt

Fachgebiet
Raumfahrttechnik

Official Documentation - WP400 SIERRA BEEGND
Project SatCom 2021

Version:
Date:
Page:
Author:

0.1
August 13, 2021
9 / 20
SatCom 2021

Figure 400.8: Mount Prototype

Mount interface design methodology

Design of mount is inspired from lathe chuck which has mechanism to hold any work-piece. In this design similar capability is achieved by providing 8 nut bolts which can hold tripod of 10 mm to 40 mm diameter. Further this design has capability to compensate levelling of rotator with respect to horizon by 10 deg. on each side. Following figure shows mount and itâC™s connection differential gear.

Figure 400.9: Mount image CAD

Luft- und Raumfahrt

Fachgebiet
Raumfahrttechnik

Official Documentation - WP400 SIERRA BEEGND
Project SatCom 2021

Version:
Date:
Page:
Author:

0.1
August 13, 2021
10 / 20
SatCom 2021

Scope of improvements

Other mounting options can be explored to reduce the cost and complexity of the design. These improvement can be implemented by using off the shelf technologies. One of the option is usage of sound box adaptor for mount as shown in figure 400.10.


Figure 400.10: Example of off shelf technology

400.3.1.4 Counter weights

Arm weight balancing

After deciding on the section of the boom that would be fixed to the rotator, we proceeded to determine the required force and its location to neutralize the weight acting on the antenna arm for this pivot point. We found the center of gravity of the antenna and then commenced moving it backwards until it sits at the center of the upper plate where it is mounted. A mass of 0.8 kg was calculated to be required at 13.5 cm from the center (from center to center). This value varies slightly depending on the shape of the weight attached. Conveniently, we found some microphone boom weights with the same value and that also attach to the same diameter of the boom we have. However sometimes an adapter might be required, and this would have slight implications on the position of the counterweight as we take into account the additional mass in that location. Figures 400.11 and 400.12 show the counter weight options.

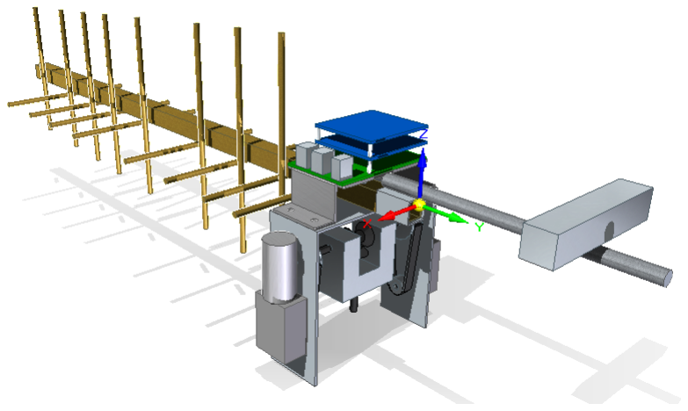
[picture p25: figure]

Figure 400.11: Arm weight balancing

Luft- und Raumfahrt

Fachgebiet
Raumfahrttechnik

Official Documentation - WP400 SIERRA BEEGND
Project SatCom 2021

Version:
Date:
Page:
Author:

0.1
August 13, 2021
11 / 20
SatCom 2021


Figure 400.12: Commercial 0.8 kg counter weight. [2]

Pitch mass shift compensation

Pitch mass shift counter weights are used to balance the centre of gravity in vertical axis. The final target is to balance centre of gravity at rotational axis of the rotator. This will put negligible load on motors and motors have to overcome just inertia. The considered rotator design requires balancing of centre of gravity in both horizontal and vertical axis. To compensate real case variations, dead weights are mounted on COTS threaded rods. This helps the user to balance the centre of gravity with extreme accuracy. Figure 400.13 shows the pitch mass weights.


Figure 400.13: Pitch mass weights

Luft- und Raumfahrt

Fachgebiet
Raumfahrttechnik

Official Documentation - WP400 SIERRA BEEGND
Project SatCom 2021

Version:
Date:
Page:
Author:

0.1
August 13, 2021
12 / 20
SatCom 2021

### 400.3.2 Electronics

The custom rotator is controlled by a Raspberry Pi, extended by a custom Raspberry Pi hat. The hat provides functionality to read the safety switches, communicate to two independent magnetic encoders, drive both motors, and monitor the motors speed with a quadrature encoder. The Hat also features an EEPROM, which is specified by the Raspberry Pi foundation, to call it an ’official’ pi hat. The pi and both motors are powered through an of the shelf power over Ethernet (POE) adapter.

400.3.2.1 choice of electronics

We had a working prototype within the first couple of weeks, which enabled us to test lots of features early on. In the beginning, we needed three cables to power the Raspberry Pi, the motors, as well as to provide a data cable for communication. The power over Ethernet adapter allowed us to only have one cable and simplify the design. To move away from our original breadboard design connected to some of the shelves components, we also designed our Raspberry Pi hat.

400.3.2.2 how to connect, pinout

The motors we used had a standard female header with a 2.54 mm pitch. We decided to stick with these connectors and used a standard female header for all connections. These female headers can be plugged into the matching male header on the PCB. All Connectors match the same side as the USB/ Ethernet etc. connections on the Raspberry Pi. That’s to make the overall cable management simpler and cleaner. The connectors are stacked on top. The board can drive two motors. One motor can be plugged in to the upper row, and the other on the lower row. The three switches are stacked on each other in the same way.

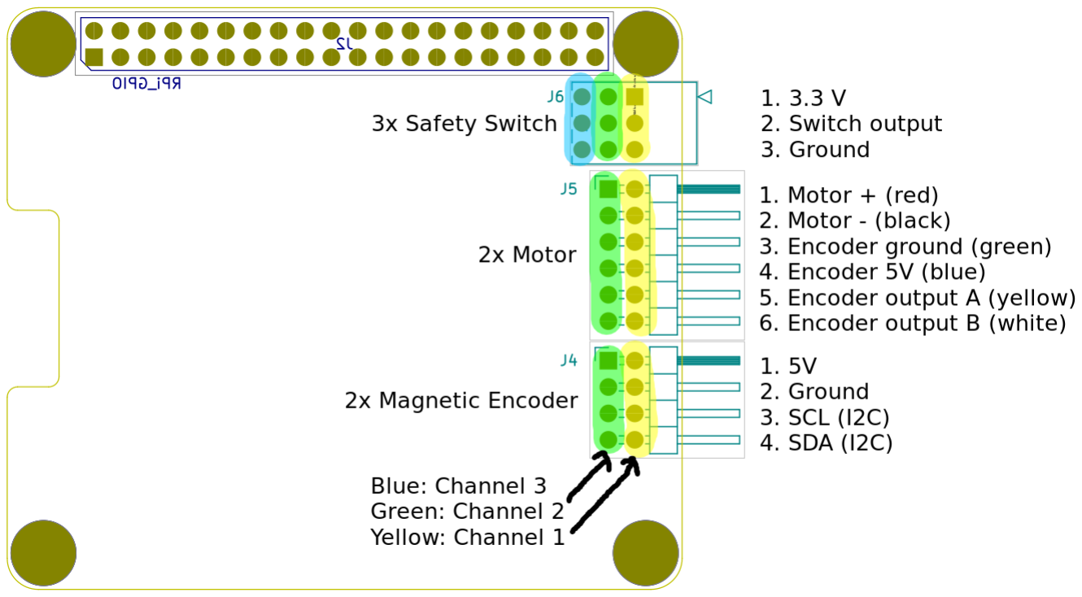
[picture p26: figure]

Figure 400.14: Raspberry Pi hat pinout

Luft- und Raumfahrt

Fachgebiet
Raumfahrttechnik

Official Documentation - WP400 SIERRA BEEGND
Project SatCom 2021

Version:
Date:
Page:
Author:

0.1
August 13, 2021
13 / 20
SatCom 2021

400.3.2.3 Electronic Design

The Raspberry Pi controls all components on the pi hat. The h-bridge, that drives the Motors, is powered externally with a 12V power source from the power over Ethernet hat. The encoder from the motors are connected through a level shifter to the Raspberry Pi. The Switches, on the other hand, are connected to the pi directly. The magnetic encoder both use the same i2c protocol. Unfortunately, they have the same address, which can’t be changed. If both encoder, are put on the same i2c bus, the pi couldn’t differentiate between those two, because they use the same address. The board features therefore an i2c multiplexer, which can select on encoder at a time. The i2c multiplexer is controlled by the same i2c bus. This reduces complexity on the board, but increases complexity in the code. The following diagram shows the structure.

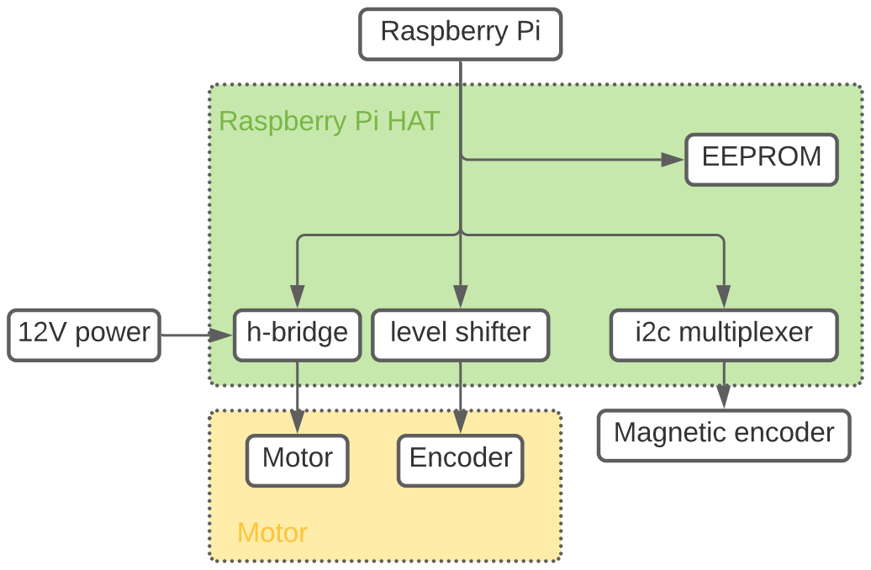
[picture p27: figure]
Magnetic encoder; Motor; 12V power; Raspberry Pi; h-bridge; i2c multiplexer; Encoder; level shifter; EEPROM; Raspberry Pi HAT

Figure 400.15: Raspberry Pi HAT block diagram

400.3.2.4 development and fabrication

We used KiCad to design the PCB. To solder the SMD components (IC’s, resistors, capacitors etc.) of the PCB, we used a soldering a reflow oven. The remaining THT components (pin headers etc.) were soldered manually. The schematic, the final pcb, as well as the manufactureing process in the reflow oven are listed in the appendix.

Luft- und Raumfahrt

Fachgebiet
Raumfahrttechnik

Official Documentation - WP400 SIERRA BEEGND
Project SatCom 2021

Version:
Date:
Page:
Author:

0.1
August 13, 2021
14 / 20
SatCom 2021

### 400.3.3 Code

400.3.3.1 Quick start

The code is executed by the Raspberry Pi. The python script needs to be started manually. For example, you could connect to the pi via ssh on the command line. If you know the IP address of the Raspberry Pi, you can log in via (default password is ’raspberry’):

ssh pi@ipAdress

If you don’t know your Raspberry Pi’s IP address, you can connect the raspberry’s Ethernet cable directly to your pc. See this Guide (https://www.circuitbasics.com/how-to-connect-to-a-raspberry-pi-directly-with-an-ethernet-cable/) or this Guide. (https://stackoverflow.com/questions/16040128/hook-up-raspberry-pi-via-ethernet-to-laptop-without-router) If you set up the Raspberry Pi for the first time, note the src/README.md in the git repository. (https://github.com/EagleEyeElite/satelliteReceiver) Once you are logged in, start the rotctl service:

source ./venv/bin/activate
cd satelliteReceiver/src/
./main.py | # start controller

Connect to the started rotctl service from your pc:

rotctl -m 2 -r 10.42.0.101:4533

400.3.3.2 Code structure

The code implements the rotctl server. It’s multithreaded to serve the clients requests and oversee the rotator simultaneously. The rotator uses two magnetic encoders, connected to the differential, to gain absolute position (even after power cut off). The motor’s encoder are used to monitor the motor speed. Additionally, the rotor can observe three safety switches to cut off the motors to prevent the rotator damaging itself. The code structure represents the structure of the rotator and the electronics. All IC’s like the h-bridge, the i2c multiplexer etc. have their own driver modules. The rotator itself and the two shafts connected to the differential are also represented as objects. Note 400.16 to see the full code structure:

Luft- und Raumfahrt

Fachgebiet
Raumfahrttechnik

Official Documentation - WP400 SIERRA BEEGND
Project SatCom 2021

Version:
Date:
Page:
Author:

0.1
August 13, 2021
15 / 20
SatCom 2021

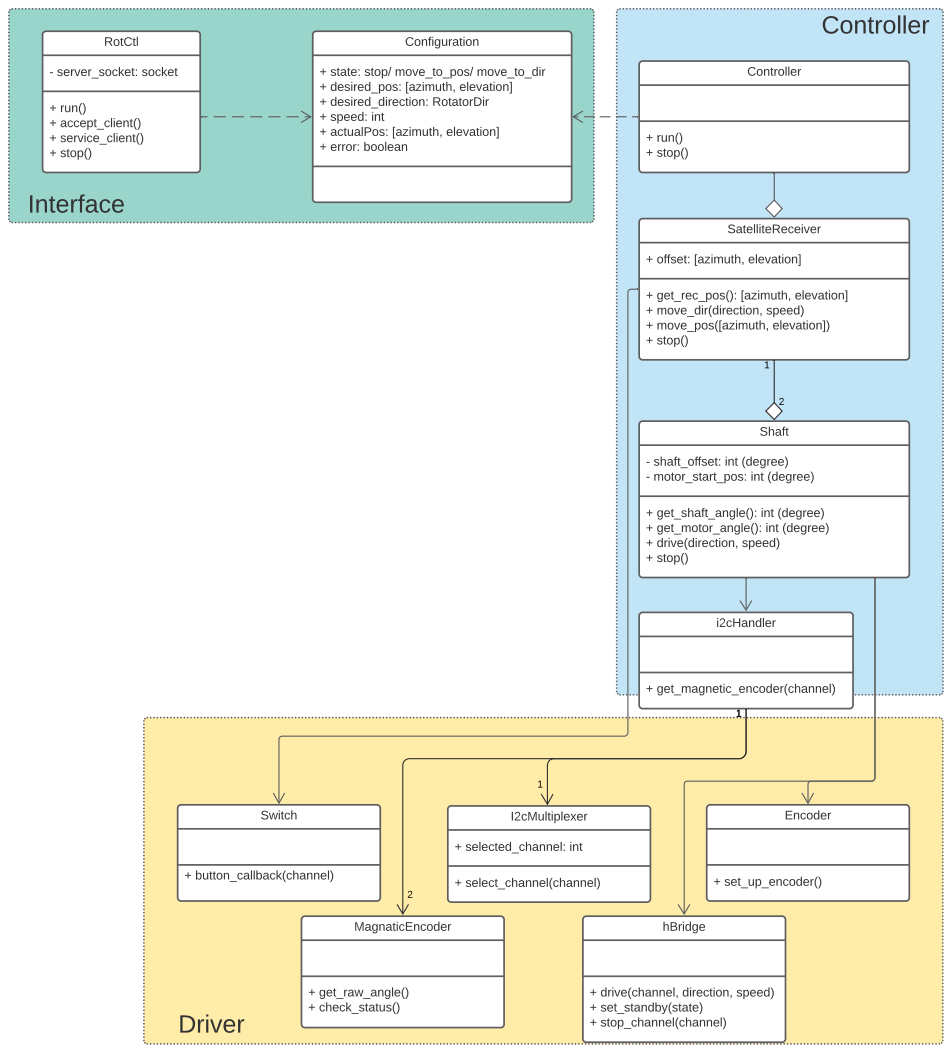
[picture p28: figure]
SatelliteReceiver; + offset: [azimuth, elevation]; + get_rec_pos(): [azimuth, elevation] + move_dir(direction, speed) + move_pos([azimuth, elevation]) + stop(); Controller; + run() + stop(); Configuration; + state: stop/ move_to_pos/ move_to_dir + desired_pos: [azimuth, elevation] + desired_direction: RotatorDir + speed: int + actualPos: [azimuth, elevation] + error: boolean; RotCtl; - server_socket: socket; + run() + accept_client() + service_client() + stop(); Shaft; - shaft_offset: int (degree) - motor_start_pos: int (degree)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

Figure 400.16: Code structure

Once the python script is started, two independent threads are started. One thread handles all communication to different clients, and the other thread handles the movement of the controller. They interact through a configuration object. The rotctl sets a desired position, direction or a stop signal. It also reads out the current actual position of the rotator. The Controller on the other hand read out the desired position, direction and the stop signal and sets the actual position. This separation allows the rotctl server to be non-blocking.
If the client requests position A and then quickly request position B, the rotator doesn’t need to wait until it moved to position A to then move the position B. With this separation it can simply discard the old request and move to the new request immediately.

Luft- und Raumfahrt

Fachgebiet
Raumfahrttechnik

Official Documentation - WP400 SIERRA BEEGND
Project SatCom 2021

Version:
Date:
Page:
Author:

0.1
August 13, 2021
16 / 20
SatCom 2021

All values in the configuration object are always updated by only one thread. The values are also not used for further computation. Even though racing condition can occur, the code is still

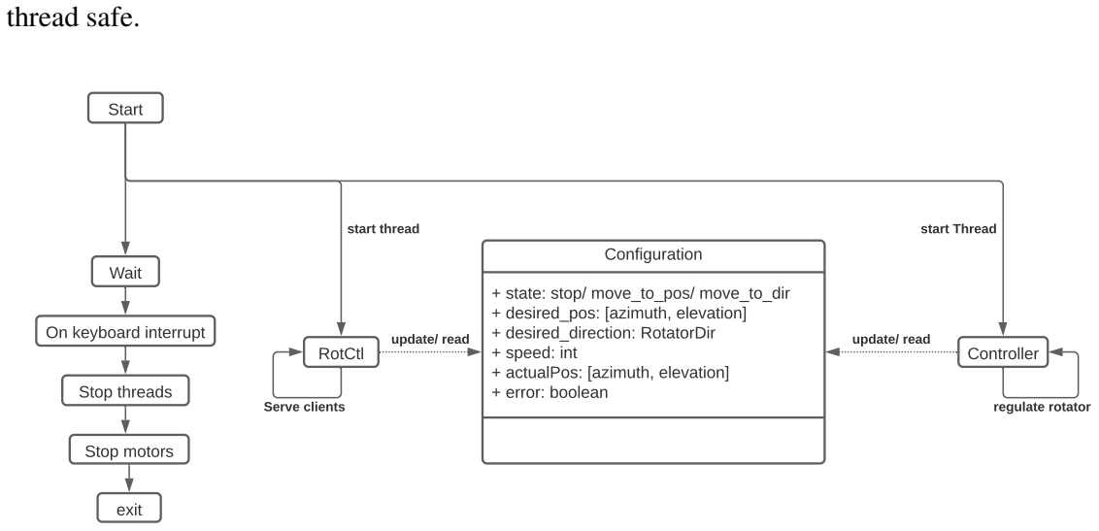
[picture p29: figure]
thread safe.; Start; RotCtl; Controller; Configuration; + state: stop/ move_to_pos/ move_to_dir + desired_pos: [azimuth, elevation] + desired_direction: RotatorDir + speed: int + actualPos: [azimuth, elevation] + error: boolean; start thread; start Thread; update/ read; Wait; Serve clients; regulate rotator; On keyboard interrupt; Stop threads; Stop motors; exit

Figure 400.17: Raspberry Pi HAT flow diagram

400.3.3.3 Possible improvements

The time constrains didn’t allow to make any real use of the EEPROM on the pi hat. With more time, it would be possible to save a configuration on that EEPROM, to set up pi the pi automatically. The I2C bus, for example, could be enabled, as soon as the board is plugged in. In a demonstration video, we showed the movement of the rotator. The readings of all sensors work well. Unfortunately, more testing is required on the position calculation. As of now, we still assume some bugs in the algorithm to get the current position. The safety switches are included in the code, but not yet on the actual rotator. It’s effortless to stop the rotator at any given time per command over rotctl or over the ssh connection. Playing around with it doesn’t introduce a huge risk. But we don’t recommend putting it up somewhere and to expect, that it doesn’t break itself eventually.

Luft- und Raumfahrt

Fachgebiet
Raumfahrttechnik

Official Documentation - WP400 SIERRA BEEGND
Project SatCom 2021

Version:
Date:
Page:
Author:

0.1
August 13, 2021
17 / 20
SatCom 2021

## 400.4 Conclusion

We enjoyed working on the project and learned a lot. The rotator is great to play around and see it in action. It’s not yet in a state, where you can put it anywhere and expect it to work perfectly. If you just want to have something working, that you don’t have to worry about and fix from time to time, we recommend using an off the shelf rotator.

Luft- und Raumfahrt

Fachgebiet
Raumfahrttechnik

Official Documentation - WP400 SIERRA BEEGND
Project SatCom 2021

Version:
Date:
Page:
Author:

0.1
August 13, 2021
18 / 20
SatCom 2021

# 500 Appendix

## 500.1 PCB schematic and manufacturing process


Figure 500.1: Schematic of Raspberry Pi hat

Luft- und Raumfahrt

Fachgebiet
Raumfahrttechnik

Official Documentation - WP400 SIERRA BEEGND
Project SatCom 2021

Version:
Date:
Page:
Author:

0.1
August 13, 2021
19 / 20
SatCom 2021

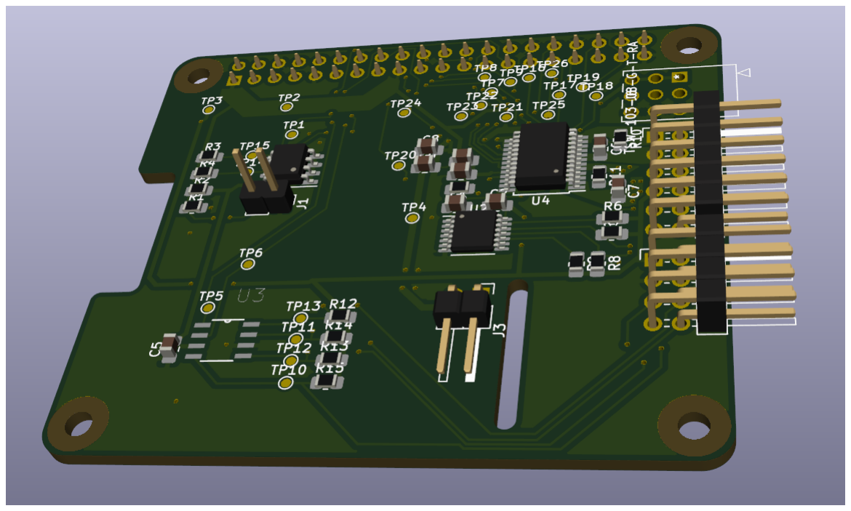
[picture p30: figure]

Figure 500.2: PCB of Raspberry Pi hat


Figure 500.3: Raspberry Pi hat manufacturing in the reflow oven

Luft- und Raumfahrt

Fachgebiet
Raumfahrttechnik

Official Documentation - WP400 SIERRA BEEGND
Project SatCom 2021

Version:
Date:
Page:
Author:

0.1
August 13, 2021
20 / 20
SatCom 2021

# Bibliography

[1] https://www.sdp-si.com/D265/PDF/D265T003.pdf
[2] https://www.k-m.de/en/kmPdf/datasheet/ordernumber/21105-000-55

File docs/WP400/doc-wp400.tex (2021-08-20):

%%%%%%%%%%%%%%%%%%%%%%%%%%%%%%%%%%%%%%%%%%%%%%%%%%%%%%%%%%%%%%%%%%%%%%%%%%%%%%%
%
% Space Rover Document
%
%%%%%%%%%%%%%%%%%%%%%%%%%%%%%%%%%%%%%%%%%%%%%%%%%%%%%%%%%%%%%%%%%%%%%%%%%%%%%%%

\newcommand{\st}{Official Documentation - WP400\\
	SIERRA BEEGND \\
	Project SatCom 2021}       % Kurzform des Titels
\newcommand{\nr}{SatCom-21-Doc-WP400}       % Dokumentennummer
\newcommand{\ver}{0.1}                      % Version
\newcommand{\dat}{\today}                   % Datum

\input{"../texdata/format_en"}
\DeclareOldFontCommand{\sl}{\normalfont\slshape}{\@nomath\sl}
\graphicspath{{../img/}{../texdata/}}    %% Suchpfad für Abbildungen
\usepackage{tocloft}
\usepackage{hyperref}
\newcommand{\mailto}[1]{\href{mailto:#1}{#1}}
\renewcommand\cftchapnumwidth{2.8em}
\begin{document}
	\renewcommand{\thisauthor}{SatCom 2021}
	\input{title}
	
	\clearpage
	
	%%%% INHALT %%%%
	\pagenumbering{Roman}
	\addcontentsline{toc}{chapter}{Table of Contents}
	\tableofcontents
	\newpage
	\listoffigures
	
	\subpdfbookmark{Contents}{tables}
	\belowpdfbookmark{Contents}{toc}
	
	\clearpage
	\def\thechapter{\arabic{chapter}00}
	\setcounter{chapter}{3}
	\chapter{Portable Rotator Concept}
	\pagenumbering{arabic}
	
	%%%%%%%%%%%%%%%%%%%%%%%%%%%%%%%%%%%%
	% your documentation here
	%%%%%%%%%%%%%%%%%%%%%%%%%%%%%%%%%%%%
	
	\section*{Abstract}
	\addcontentsline{toc}{section}{Abstract}
	
	This report demonstrates an overview of the planning process and work carried out throughout the semester by the team to design and build a new antenna rotator concept.
	
	\section{Introduction}
Various rotators are available and used in controlling the attitude of different types of antennas. For this project the motivation is to develop a new concept to be used with a portable station and able to track satellites, and to achieve this it is designed to move in both azimuth and elevation directions. To meet the requirements, the rotator is characterized by being low cost and based on commercial off-the-shelf parts to compete with available models on the market. \\
The idea is to have a transportable and remotely controllable rotator to test the signal strength of telemetry data that is received in different locations from satellites in a low earth orbits.\\
This concept can be replicated by other interested individuals and is open for improvements. \\
The sections of the report are divided into mechanical and electronic design of the product and covers its calibration and testing plan.

	\section{Project Planning}
	\input{planning}
	
	\section{Project Work}
	
	\subsection{Mechancial}
	\input{Rotator head}
	\input{Weather shield}
    \input{Mount interface}	
    \input{Counter weights}

	\include{electronics}
	\include{code}

	\section{Conclusion}
	We enjoyed working on the project and learned a lot. The rotator is great to play around and see it in action. It's not yet in a state, where you can put it anywhere and expect it to work perfectly. If you just want to have something working, that you don't have to worry about and fix from time to time, we recommend using an off the shelf rotator.
	
	\chapter{Appendix}
	\input{appendix.tex}
	\newpage
	
\bibliographystyle{alpha}
\bibliography{sample}
\input{biblo}

\end{document}

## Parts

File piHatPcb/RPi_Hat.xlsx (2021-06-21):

Prj: | Satellite receiver controller |  |  |  | Board Qty: | 100
Co.: |  |  |  |  | Unit Cost: | $0.00
Prj date: | Di 15 Jun 2021 12:57:25 CEST |  |  |  | Total Cost: | $0.00 |  |  |  | $0.00 | 0 |  |  |  | $0.00 | 0 |  |  |  | $0.00 | 0 |  |  |  | $0.00 | 0 |  |  |  | $0.00 | 0 |  |  |  | $0.00 | 0 |  |  |  | $0.00 | 0 |  |  |  | $0.00 | 0
$ date: | 2021-06-15 12:57:29
Global Part Info |  |  |  |  |  |  | Arrow |  |  |  |  | Digi-Key |  |  |  |  | Farnell |  |  |  |  | LCSC |  |  |  |  | Mouser |  |  |  |  | Newark |  |  |  |  | RS Components |  |  |  |  | TME
Refs | Value | Footprint | Manf# | Qty | Unit$ | Ext$ | Avail | Purch | Unit$ | Ext$ | Cat# | Avail | Purch | Unit$ | Ext$ | Cat# | Avail | Purch | Unit$ | Ext$ | Cat# | Avail | Purch | Unit$ | Ext$ | Cat# | Avail | Purch | Unit$ | Ext$ | Cat# | Avail | Purch | Unit$ | Ext$ | Cat# | Avail | Purch | Unit$ | Ext$ | Cat# | Avail | Purch | Unit$ | Ext$ | Cat#
C4,C9 | 10u | C_0805_2012Metric_Pad1.18x1.45mm_HandSolder | CL21A106KOQNNNE | 0 | $0.00 | $0.00 |  |  |  |  |  | 193579 |  | $0.00 | $0.00 | 1276-1096-1-ND (https://octopart.com/click/track?ai=8078&sig=094a57f&sid=459&ppid=12262895&vpid=72525729&ct=offers) | 44000 |  | $0.00 | $0.00 | 3013453 (https://octopart.com/click/track?ai=8078&sig=079c748&sid=819&ppid=12262895&vpid=541437365&ct=offers) | 3849650 |  | $0.00 | $0.00 | C1713 (https://octopart.com/click/track?ai=8078&sig=0f23b52&sid=27971&ppid=12262895&vpid=476994733&ct=offers) | 123404 |  | $0.00 | $0.00 | 187CL21A106KOQNNNE (https://octopart.com/click/track?ai=8078&sig=0dac06a&sid=2401&ppid=12262895&vpid=658751393&ct=offers) | 142000 |  | $0.00 | $0.00 | 82AC9389 (https://octopart.com/click/track?ai=8078&sig=06b776e&sid=2402&ppid=12262895&vpid=511545699&ct=offers) |  |  |  |  |  | 267200 |  | $0.00 | $0.00 | CL21A106KOQNNNE (https://octopart.com/click/track?ai=8078&sig=024c141&sid=1532&ppid=12262895&vpid=709157373&ct=offers)
C6,C7 | DNP | C_0805_2012Metric_Pad1.18x1.45mm_HandSolder |  | 0 | $0.00 | $0.00
C1-C3,C5,C8 | 0.1u | C_0805_2012Metric_Pad1.18x1.45mm_HandSolder | 08055C104KAT2A | 0 | $0.00 | $0.00 |  |  |  |  |  | 8474868 |  | $0.00 | $0.00 | 478-1395-1-ND (https://octopart.com/click/track?ai=8078&sig=01b1845&sid=459&ppid=55386349&vpid=187969502&ct=offers) | 9368000 |  | $0.00 | $0.00 | 4765801 (https://octopart.com/click/track?c=1&ai=8078&sig=04fe7cc&sid=11744&ppid=55386349&vpid=237113689&ct=offers) |  |  |  |  |  | 1722573 |  | $0.00 | $0.00 | 58108055C104K (https://octopart.com/click/track?ai=8078&sig=09c60b9&sid=2401&ppid=55386349&vpid=187733814&ct=offers) | 10568000 |  | $0.00 | $0.00 | 27C8438 (https://octopart.com/click/track?ai=8078&sig=04f49ed&sid=2402&ppid=55386349&vpid=190823978&ct=offers) | 10050 |  | $0.00 | $0.00 | 4646688 (https://octopart.com/click/track?ai=8078&sig=082b5da&sid=10022&ppid=55386349&vpid=198971583&ct=offers) | NonStk |  | $0.00 | $0.00 | 08055C104KAT2A (https://octopart.com/click/track?ai=8078&sig=0582845&sid=1532&ppid=55386349&vpid=707794437&ct=offers)
H1-H4 | 3mm_Mounting_Hole | RPi_Hat_Mounting_Hole |  | 0 | $0.00 | $0.00
J1 | CONN_01X02 | PinHeader_1x02_P2.54mm_Vertical | 77311-118-02LF (http://datasheet.octopart.com/77311-118-02LF-Amphenol-ICC-datasheet-5394197.pdf) | 0 | $0.00 | $0.00 |  |  |  |  |  | 23963 |  | $0.00 | $0.00 | 609-4434-ND (https://octopart.com/click/track?ai=8078&sig=02848dd&sid=459&ppid=90334053&vpid=531264172&ct=offers) | 1666 |  | $0.00 | $0.00 | 1622283 (https://octopart.com/click/track?c=1&ai=8078&sig=0944837&sid=11744&ppid=90334053&vpid=477210439&ct=offers) |  |  |  |  |  | 3386 |  | $0.00 | $0.00 | 6497731111802LF (https://octopart.com/click/track?ai=8078&sig=074cc9a&sid=2401&ppid=90334053&vpid=120232497&ct=offers) | 2892 |  | $0.00 | $0.00 | 62K8865 (https://octopart.com/click/track?ai=8078&sig=0c83c55&sid=2402&ppid=90334053&vpid=474120831&ct=offers)
J2 | RPi_GPIO | PinSocket_2x20_P2.54mm_Vertical | PPPC202LFBN-RC (http://datasheet.octopart.com/PPPC202LFBN-RC-Sullins-datasheet-12463.pdf) | 0 | $0.00 | $0.00 |  |  |  |  |  | 28339 |  | $0.00 | $0.00 | S7123-ND (https://octopart.com/click/track?ai=8078&sig=06feed1&sid=459&ppid=271136&vpid=1910538&ct=offers)
J3 | 12V in | PinHeader_1x02_P2.54mm_Horizontal | PH1RB-02-UA | 0 | $0.00 | $0.00 |  |  |  |  |  | 3540 |  | $0.00 | $0.00 | 2057-PH1RB-02-UA-ND (https://octopart.com/click/track?ai=8078&sig=0ac5109&sid=459&ppid=76895609&vpid=523310284&ct=offers)
J4 | Conn_02x04_Row_Letter_First | PinHeader_2x04_P2.54mm_Horizontal | PH2RA-08-UA | 0 | $0.00 | $0.00 |  |  |  |  |  | 2137 |  | $0.00 | $0.00 | 2057-PH2RA-08-UA-ND (https://octopart.com/click/track?ai=8078&sig=095c6ca&sid=459&ppid=23529466&vpid=523310392&ct=offers)
J5 | Conn_02x06_Row_Letter_First | PinHeader_2x06_P2.54mm_Horizontal | PH2RA-12-UA | 0 | $0.00 | $0.00 |  |  |  |  |  | 1081 |  | $0.00 | $0.00 | 2057-PH2RA-12-UA-ND (https://octopart.com/click/track?ai=8078&sig=07acce4&sid=459&ppid=76895625&vpid=523310394&ct=offers)
J6 | TSW-103-08-G-T-RA | TSW-103-08-G-T-RA | TSW-103-08-G-T-RA (https://www.digikey.de/product-detail/en/samtec-inc/TSW-103-08-G-T-RA/SAM8888-ND/2685879) | 0 | $0.00 | $0.00 |  |  |  |  |  | 375 |  | $0.00 | $0.00 | SAM8888-ND (https://octopart.com/click/track?ai=8078&sig=0cf1350&sid=459&ppid=13116718&vpid=225542734&ct=offers) | NonStk |  | $0.00 | $0.00 | 2856688 (https://octopart.com/click/track?c=1&ai=8078&sig=05592c0&sid=11744&ppid=13116718&vpid=478780716&ct=offers) |  |  |  |  |  | 271 |  | $0.00 | $0.00 | 200TSW10308GTRA (https://octopart.com/click/track?ai=8078&sig=0305690&sid=2401&ppid=13116718&vpid=493296008&ct=offers) | NonStk |  | $0.00 | $0.00 | 79P4012 (https://octopart.com/click/track?c=1&ai=8078&sig=03457b7&sid=2402&ppid=13116718&vpid=47155391&ct=offers) | 22 |  | $0.00 | $0.00 | 1803136 (https://octopart.com/click/track?ai=8078&sig=043d6ae&sid=10022&ppid=13116718&vpid=510206029&ct=offers)
R1,R10,R11 | DNP | R_0805_2012Metric_Pad1.20x1.40mm_HandSolder |  | 0 | $0.00 | $0.00
R2 | 10K | R_0805_2012Metric_Pad1.20x1.40mm_HandSolder | CRCW080510K0FKEAC (https://www.mouser.de/datasheet/2/427/crcwce3-1762584.pdf) | 0 | $0.00 | $0.00 |  |  |  |  |  | 590734 |  | $0.00 | $0.00 | 541-3976-1-ND (https://octopart.com/click/track?ai=8078&sig=0d20d2d&sid=459&ppid=23798533&vpid=454353705&ct=offers) |  |  |  |  |  |  |  |  |  |  | 332906 |  | $0.00 | $0.00 | 71CRCW080510K0FKEAC (https://octopart.com/click/track?ai=8078&sig=030ab9c&sid=2401&ppid=23798533&vpid=454250937&ct=offers) | NonStk |  | $0.00 | $0.00 | 45AC9160 (https://octopart.com/click/track?c=1&ai=8078&sig=0c28739&sid=2402&ppid=23798533&vpid=462488672&ct=offers)
R3,R4 | 3.9K | R_0805_2012Metric_Pad1.20x1.40mm_HandSolder | ERA-6AED392V (https://www.mouser.de/datasheet/2/315/AOA0000C307-1149632.pdf) | 0 | $0.00 | $0.00 |  |  |  |  |  | 761 |  | $0.00 | $0.00 | P123844CT-ND (https://octopart.com/click/track?ai=8078&sig=062112f&sid=459&ppid=23424332&vpid=486714107&ct=offers) | NonStk |  | $0.00 | $0.00 | 3349992 (https://octopart.com/click/track?c=1&ai=8078&sig=0354969&sid=819&ppid=23424332&vpid=603687420&ct=offers) |  |  |  |  |  | 955 |  | $0.00 | $0.00 | 667ERA6AED392V (https://octopart.com/click/track?ai=8078&sig=04c8160&sid=2401&ppid=23424332&vpid=82053183&ct=offers) | NonStk |  | $0.00 | $0.00 | 31X0600 (https://octopart.com/click/track?c=1&ai=8078&sig=037bb70&sid=2402&ppid=23424332&vpid=120931863&ct=offers)
R12-R15 | 1.8k | R_0805_2012Metric_Pad1.20x1.40mm_HandSolder | CRGCQ0805F1K8 | 0 | $0.00 | $0.00 |  |  |  |  |  | 31094 |  | $0.00 | $0.00 | A129752CT-ND (https://octopart.com/click/track?ai=8078&sig=03b83d6&sid=459&ppid=91018157&vpid=475508703&ct=offers) | 3917 |  | $0.00 | $0.00 | 2861525 (https://octopart.com/click/track?ai=8078&sig=07f20a0&sid=819&ppid=91018157&vpid=499748033&ct=offers) |  |  |  |  |  | 10425 |  | $0.00 | $0.00 | 279CRGCQ0805F1K8 (https://octopart.com/click/track?ai=8078&sig=0ffa63e&sid=2401&ppid=91018157&vpid=478301007&ct=offers) | 2718 |  | $0.00 | $0.00 | 61AC6543 (https://octopart.com/click/track?ai=8078&sig=0164d45&sid=2402&ppid=91018157&vpid=501422191&ct=offers)
R5-R9 | 3.8k | R_0805_2012Metric_Pad1.20x1.40mm_HandSolder | PAT0805E3791BST1 | 0 | $0.00 | $0.00 |  |  |  |  |  | 656 |  | $0.00 | $0.00 | PAT3.79KBCT-ND (https://octopart.com/click/track?ai=8078&sig=02738b1&sid=459&ppid=19181223&vpid=715270735&ct=offers) |  |  |  |  |  |  |  |  |  |  | 455 |  | $0.00 | $0.00 | 71PAT0805E3791BST1 (https://octopart.com/click/track?ai=8078&sig=0167e8d&sid=2401&ppid=19181223&vpid=37944579&ct=offers)
TP1-TP26 | DIS_EL_TP | TestPoint_Pad_D1.0mm |  | 0 | $0.00 | $0.00
U1 | CAT24C32 | SOIC-8_3.9x4.9mm_P1.27mm | CAT24C32WI-GT3 (https://www.mouser.de/datasheet/2/308/CAT24C32_D-1815633.pdf) | 0 | $0.00 | $0.00 |  |  |  |  |  | 9 |  | $0.00 | $0.00 | CAT24C32WI-GT3CT-ND (https://octopart.com/click/track?ai=8078&sig=08aaa4f&sid=459&ppid=46637079&vpid=118264218&ct=offers) | 55 |  | $0.00 | $0.00 | 2463713 (https://octopart.com/click/track?ai=8078&sig=01cfe12&sid=11744&ppid=46637079&vpid=183084971&ct=offers) | 1 |  | $0.00 | $0.00 | C81193 (https://octopart.com/click/track?ai=8078&sig=053f908&sid=27971&ppid=46637079&vpid=476993061&ct=offers) | NonStk |  | $0.00 | $0.00 | 698CAT24C32WIGT3 (https://octopart.com/click/track?c=1&ai=8078&sig=0b995f7&sid=2401&ppid=46637079&vpid=458431801&ct=offers) | 11000 |  | $0.00 | $0.00 | 08R5414 (https://octopart.com/click/track?ai=8078&sig=0943c84&sid=2402&ppid=46637079&vpid=119031734&ct=offers) | 7360 |  | $0.00 | $0.00 | 7814828 (https://octopart.com/click/track?ai=8078&sig=03f07fc&sid=10022&ppid=46637079&vpid=199083826&ct=offers)
U2 | TXS0104E | TSSOP-14_4.4x5mm_P0.65mm | TXS0104ED (http://www.ti.com/lit/ds/symlink/txb0104.pdf) | 0 | $0.00 | $0.00 |  |  |  |  |  | 3351 |  | $0.00 | $0.00 | 296-34699-5-ND (https://octopart.com/click/track?ai=8078&sig=07e02d6&sid=459&ppid=1486620&vpid=52624612&ct=offers) | NonStk |  | $0.00 | $0.00 | 3006813 (https://octopart.com/click/track?c=1&ai=8078&sig=0bf7152&sid=819&ppid=1486620&vpid=575370610&ct=offers) |  |  |  |  |  | 2676 |  | $0.00 | $0.00 | 595TXS0104ED (https://octopart.com/click/track?ai=8078&sig=021d7b9&sid=2401&ppid=1486620&vpid=37755129&ct=offers) | NonStk |  | $0.00 | $0.00 | 28AH6298 (https://octopart.com/click/track?c=1&ai=8078&sig=015de3d&sid=2402&ppid=1486620&vpid=578997844&ct=offers) | 600 |  | $0.00 | $0.00 | 7093309 (https://octopart.com/click/track?ai=8078&sig=0f42075&sid=10022&ppid=1486620&vpid=199172101&ct=offers)
U3 | PCA9540BD,118 | PCA9540BD,118 | PCA9540BD 118 (https://www.mouser.de/datasheet/2/302/PCA9540B-1127423.pdf) | 0 | $0.00 | $0.00 |  |  |  |  |  | 6993 |  | $0.00 | $0.00 | 568-1844-1-ND (https://octopart.com/click/track?ai=8078&sig=0eb6a78&sid=459&ppid=10469051&vpid=34291083&ct=offers) | 3120 |  | $0.00 | $0.00 | 2890521 (https://octopart.com/click/track?ai=8078&sig=06c4672&sid=11744&ppid=10469051&vpid=489775752&ct=offers) |  |  |  |  |  | 4644 |  | $0.00 | $0.00 | 771PCA9540BDT (https://octopart.com/click/track?ai=8078&sig=0f03c55&sid=2401&ppid=10469051&vpid=37835355&ct=offers) | 3120 |  | $0.00 | $0.00 | 61AC1254 (https://octopart.com/click/track?ai=8078&sig=0d1e505&sid=2402&ppid=10469051&vpid=489660930&ct=offers)
U4 | TB6612FNG | SSOP-24_5.3x8.2mm_P0.65mm | TB6612FNG C 8 EL | 0 | $0.00 | $0.00 |  |  |  |  |  | 38460 |  | $0.00 | $0.00 | TB6612FNGC8ELCT-ND (https://octopart.com/click/track?ai=8078&sig=0c94409&sid=459&ppid=50464480&vpid=166769544&ct=offers) |  |  |  |  |  | 1692 |  | $0.00 | $0.00 | C141517 (https://octopart.com/click/track?ai=8078&sig=0366060&sid=27971&ppid=50464480&vpid=454624494&ct=offers) | 7645 |  | $0.00 | $0.00 | 757TB6612FNGC8EL (https://octopart.com/click/track?ai=8078&sig=076219f&sid=2401&ppid=50464480&vpid=240122954&ct=offers) |  |  |  |  |  |  |  |  |  |  | 1335 |  | $0.00 | $0.00 | TB6612FNG (https://octopart.com/click/track?ai=8078&sig=0149495&sid=1532&ppid=50464480&vpid=709231210&ct=offers)
 | Used currency rates: |  |  |  | Total Purchase: | $0.00 |  | 0 |  | $0.00 |  |  | 0 |  | $0.00 |  |  | 0 |  | $0.00 |  |  | 0 |  | $0.00 |  |  | 0 |  | $0.00 |  |  | 0 |  | $0.00 |  |  | 0 |  | $0.00 |  |  | 0 |  | $0.00
 | USD($)/GBP(£): | 1.414654066 |  |  | Purchase description: |  |  | 0 |  |  |  |  | 0 |  |  |  |  | 0 |  |  |  |  | 0 |  |  |  |  | 0 |  |  |  |  | 0 |  |  |  |  | 0 |  |  |  |  | 0
 |  |  |  |  |  |  |  | 0 |  |  |  |  | 0 |  |  |  |  | 0 |  |  |  |  | 0 |  |  |  |  | 0 |  |  |  |  | 0 |  |  |  |  | 0 |  |  |  |  | 0
KiCost® v.1.1.4 |  |  |  |  |  |  |  | 0 |  |  |  |  | 0 |  |  |  |  | 0 |  |  |  |  | 0 |  |  |  |  | 0 |  |  |  |  | 0 |  |  |  |  | 0 |  |  |  |  | 0
 |  |  |  |  |  |  |  | 0 |  |  |  |  | 0 |  |  |  |  | 0 |  |  |  |  | 0 |  |  |  |  | 0 |  |  |  |  | 0 |  |  |  |  | 0 |  |  |  |  | 0
 |  |  |  |  |  |  |  | 0 |  |  |  |  | 0 |  |  |  |  | 0 |  |  |  |  | 0 |  |  |  |  | 0 |  |  |  |  | 0 |  |  |  |  | 0 |  |  |  |  | 0
 |  |  |  |  |  |  |  | 0 |  |  |  |  | 0 |  |  |  |  | 0 |  |  |  |  | 0 |  |  |  |  | 0 |  |  |  |  | 0 |  |  |  |  | 0 |  |  |  |  | 0
 |  |  |  |  |  |  |  | 0 |  |  |  |  | 0 |  |  |  |  | 0 |  |  |  |  | 0 |  |  |  |  | 0 |  |  |  |  | 0 |  |  |  |  | 0 |  |  |  |  | 0
 |  |  |  |  |  |  |  | 0 |  |  |  |  | 0 |  |  |  |  | 0 |  |  |  |  | 0 |  |  |  |  | 0 |  |  |  |  | 0 |  |  |  |  | 0 |  |  |  |  | 0
 |  |  |  |  |  |  |  | 0 |  |  |  |  | 0 |  |  |  |  | 0 |  |  |  |  | 0 |  |  |  |  | 0 |  |  |  |  | 0 |  |  |  |  | 0 |  |  |  |  | 0
 |  |  |  |  |  |  |  | 0 |  |  |  |  | 0 |  |  |  |  | 0 |  |  |  |  | 0 |  |  |  |  | 0 |  |  |  |  | 0 |  |  |  |  | 0 |  |  |  |  | 0
 |  |  |  |  |  |  |  | 0 |  |  |  |  | 0 |  |  |  |  | 0 |  |  |  |  | 0 |  |  |  |  | 0 |  |  |  |  | 0 |  |  |  |  | 0 |  |  |  |  | 0
 |  |  |  |  |  |  |  | 0 |  |  |  |  | 0 |  |  |  |  | 0 |  |  |  |  | 0 |  |  |  |  | 0 |  |  |  |  | 0 |  |  |  |  | 0 |  |  |  |  | 0
 |  |  |  |  |  |  |  | 0 |  |  |  |  | 0 |  |  |  |  | 0 |  |  |  |  | 0 |  |  |  |  | 0 |  |  |  |  | 0 |  |  |  |  | 0 |  |  |  |  | 0
 |  |  |  |  |  |  |  | 0 |  |  |  |  | 0 |  |  |  |  | 0 |  |  |  |  | 0 |  |  |  |  | 0 |  |  |  |  | 0 |  |  |  |  | 0 |  |  |  |  | 0
 |  |  |  |  |  |  |  | 0 |  |  |  |  | 0 |  |  |  |  | 0 |  |  |  |  | 0 |  |  |  |  | 0 |  |  |  |  | 0 |  |  |  |  | 0 |  |  |  |  | 0
 |  |  |  |  |  |  |  | 0 |  |  |  |  | 0 |  |  |  |  | 0 |  |  |  |  | 0 |  |  |  |  | 0 |  |  |  |  | 0 |  |  |  |  | 0 |  |  |  |  | 0
 |  |  |  |  |  |  |  | 0 |  |  |  |  | 0 |  |  |  |  | 0 |  |  |  |  | 0 |  |  |  |  | 0 |  |  |  |  | 0 |  |  |  |  | 0 |  |  |  |  | 0
 |  |  |  |  |  |  |  | 0 |  |  |  |  | 0 |  |  |  |  | 0 |  |  |  |  | 0 |  |  |  |  | 0 |  |  |  |  | 0 |  |  |  |  | 0 |  |  |  |  | 0
 |  |  |  |  |  |  |  | 0 |  |  |  |  | 0 |  |  |  |  | 0 |  |  |  |  | 0 |  |  |  |  | 0 |  |  |  |  | 0 |  |  |  |  | 0 |  |  |  |  | 0
 |  |  |  |  |  |  |  | 0 |  |  |  |  | 0 |  |  |  |  | 0 |  |  |  |  | 0 |  |  |  |  | 0 |  |  |  |  | 0 |  |  |  |  | 0 |  |  |  |  | 0
 |  |  |  |  |  |  |  |  |  |  |  |  |  |  |  |  |  |  |  |  |  |  | 0

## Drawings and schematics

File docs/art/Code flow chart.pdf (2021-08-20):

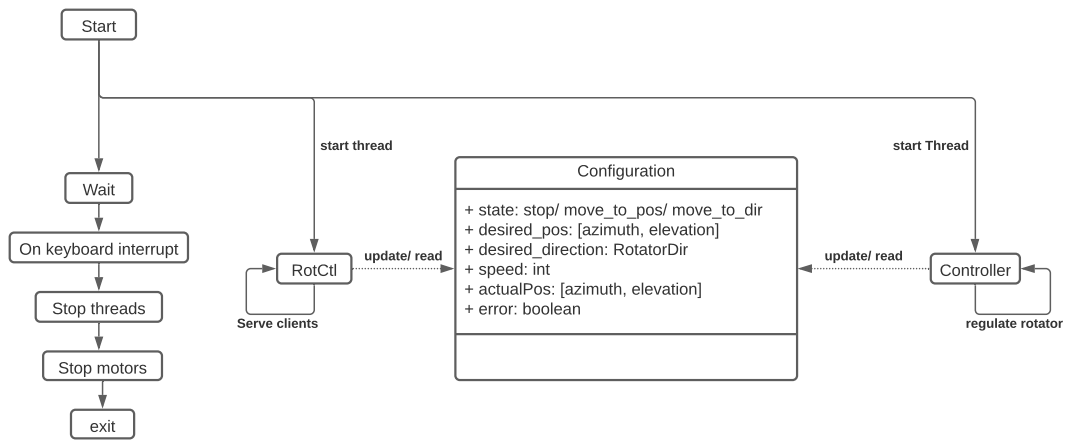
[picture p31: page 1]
Start; RotCtl; Controller; Configuration; start thread; start Thread; update/ read; Wait; Serve clients; regulate rotator; Stop threads; Stop motors; exit

+ state: stop/ move_to_pos/ move_to_dir
+ desired_pos: [azimuth, elevation]
+ desired_direction: RotatorDir
+ speed: int
+ actualPos: [azimuth, elevation]
+ error: boolean

On keyboard interrupt

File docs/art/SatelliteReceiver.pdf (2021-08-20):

# Interface

# Controller

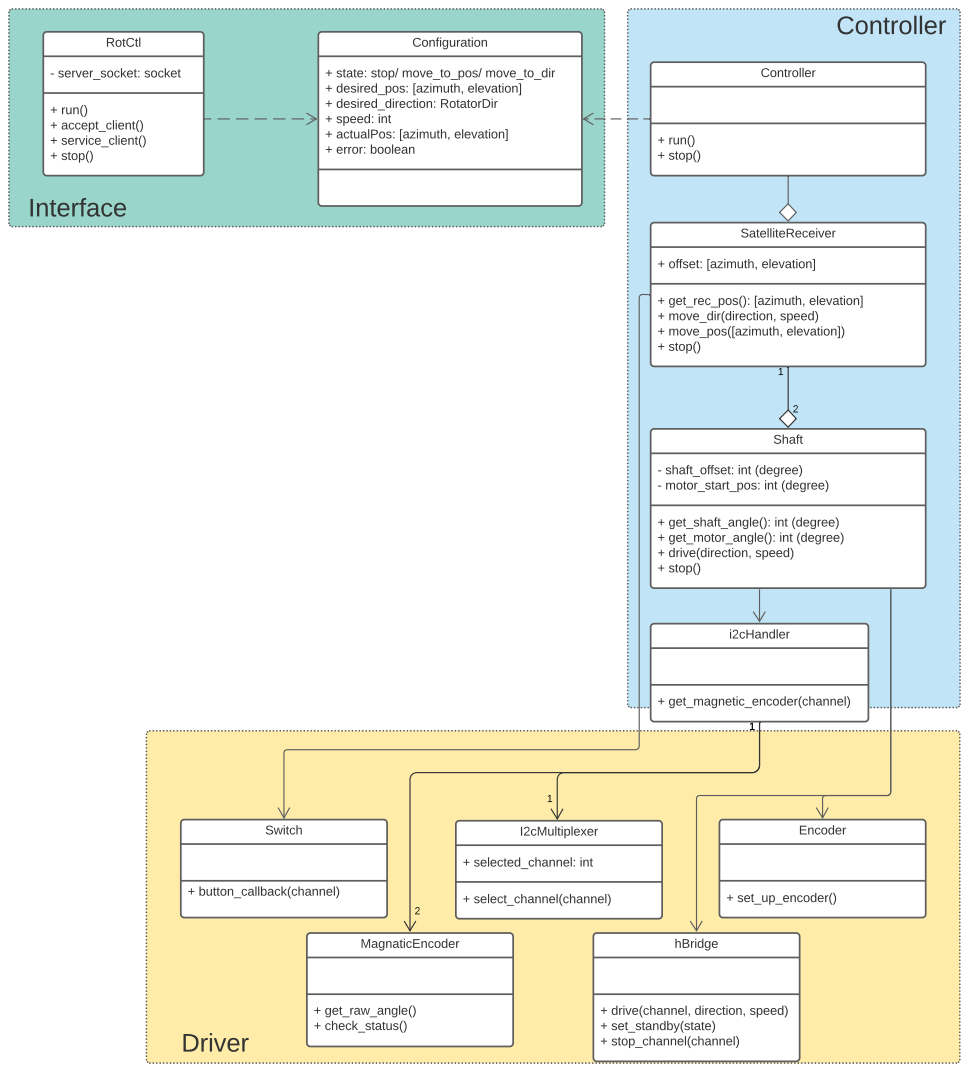
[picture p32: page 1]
SatelliteReceiver; + get_rec_pos(): [azimuth, elevation] + move_dir(direction, speed) + move_pos([azimuth, elevation]) + stop(); Controller; + run() + stop(); Configuration; RotCtl; - server_socket: socket; + run() + accept_client() + service_client() + stop(); Shaft; - shaft_offset: int (degree) - motor_start_pos: int (degree); hBridge; Encoder; + set_up_encoder(); MagnaticEncoder; + get_raw_angle() + check_status(); Switch; + button_callback(channel); i2cHandler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

+ state: stop/ move_to_pos/ move_to_dir
+ desired_pos: [azimuth, elevation]
+ desired_direction: RotatorDir
+ speed: int
+ actualPos: [azimuth, elevation]
+ error: boolean

+ offset: [azimuth, elevation]

+ get_shaft_angle(): int (degree)
+ get_motor_angle(): int (degree)
+ drive(direction, speed)
+ stop()

+ drive(channel, direction, speed)
+ set_standby(state)
+ stop_channel(channel)

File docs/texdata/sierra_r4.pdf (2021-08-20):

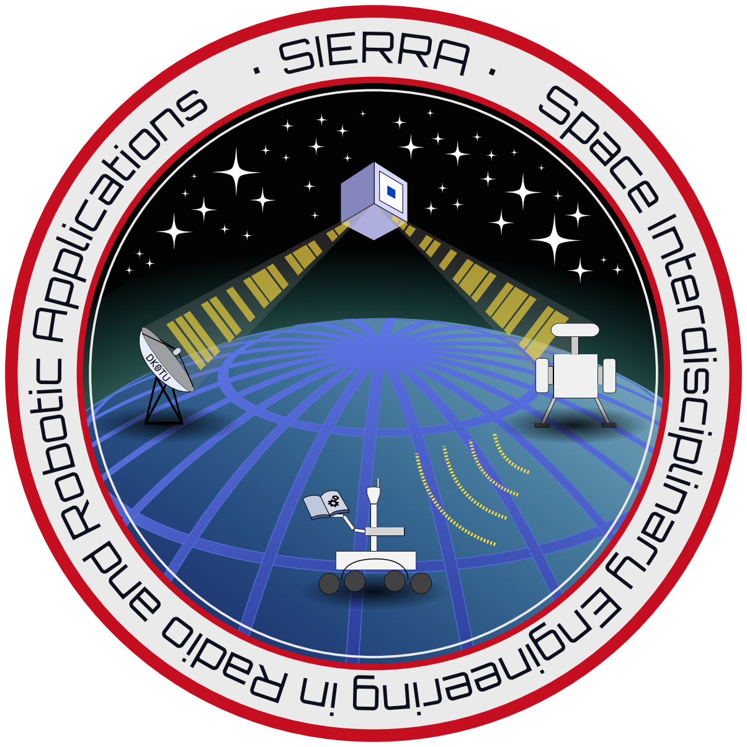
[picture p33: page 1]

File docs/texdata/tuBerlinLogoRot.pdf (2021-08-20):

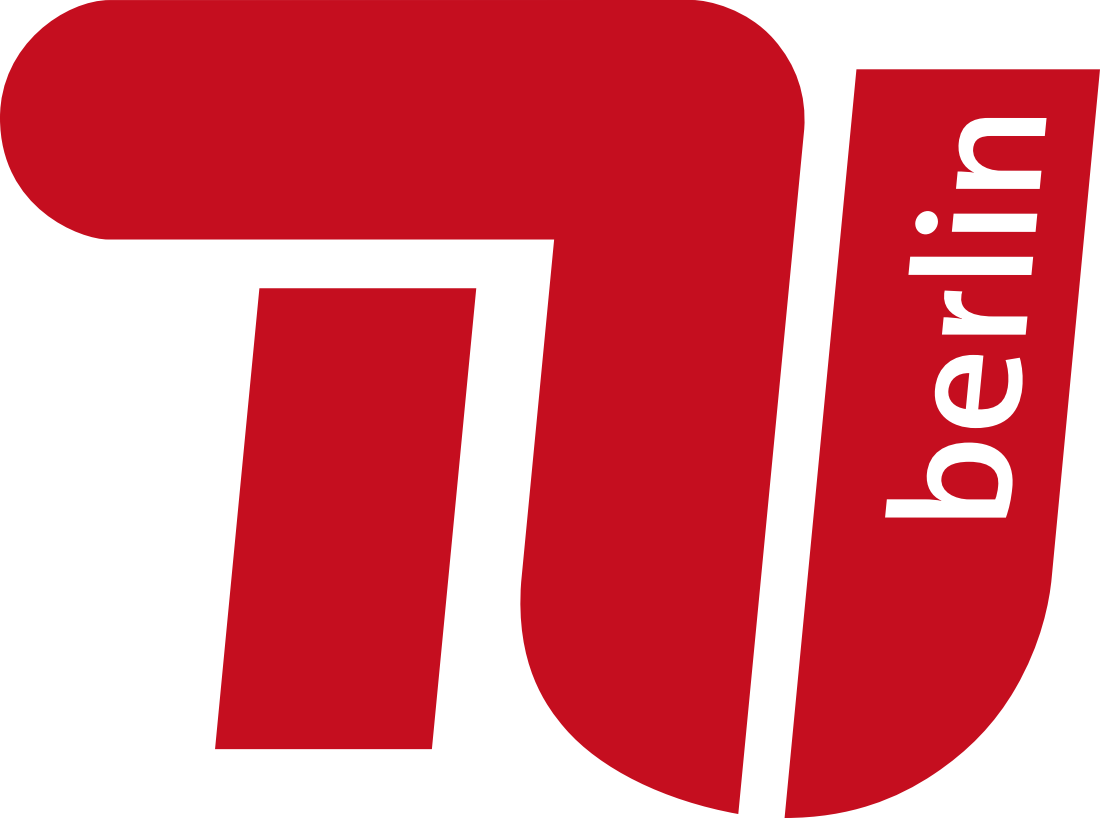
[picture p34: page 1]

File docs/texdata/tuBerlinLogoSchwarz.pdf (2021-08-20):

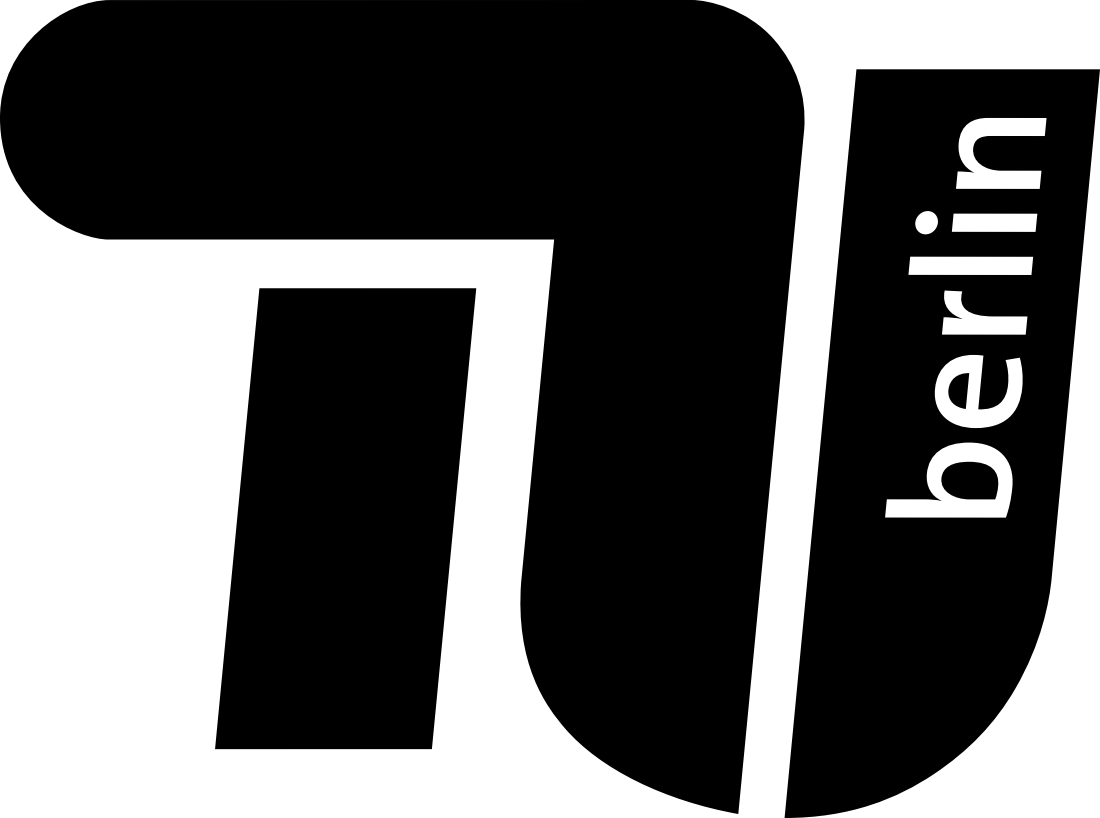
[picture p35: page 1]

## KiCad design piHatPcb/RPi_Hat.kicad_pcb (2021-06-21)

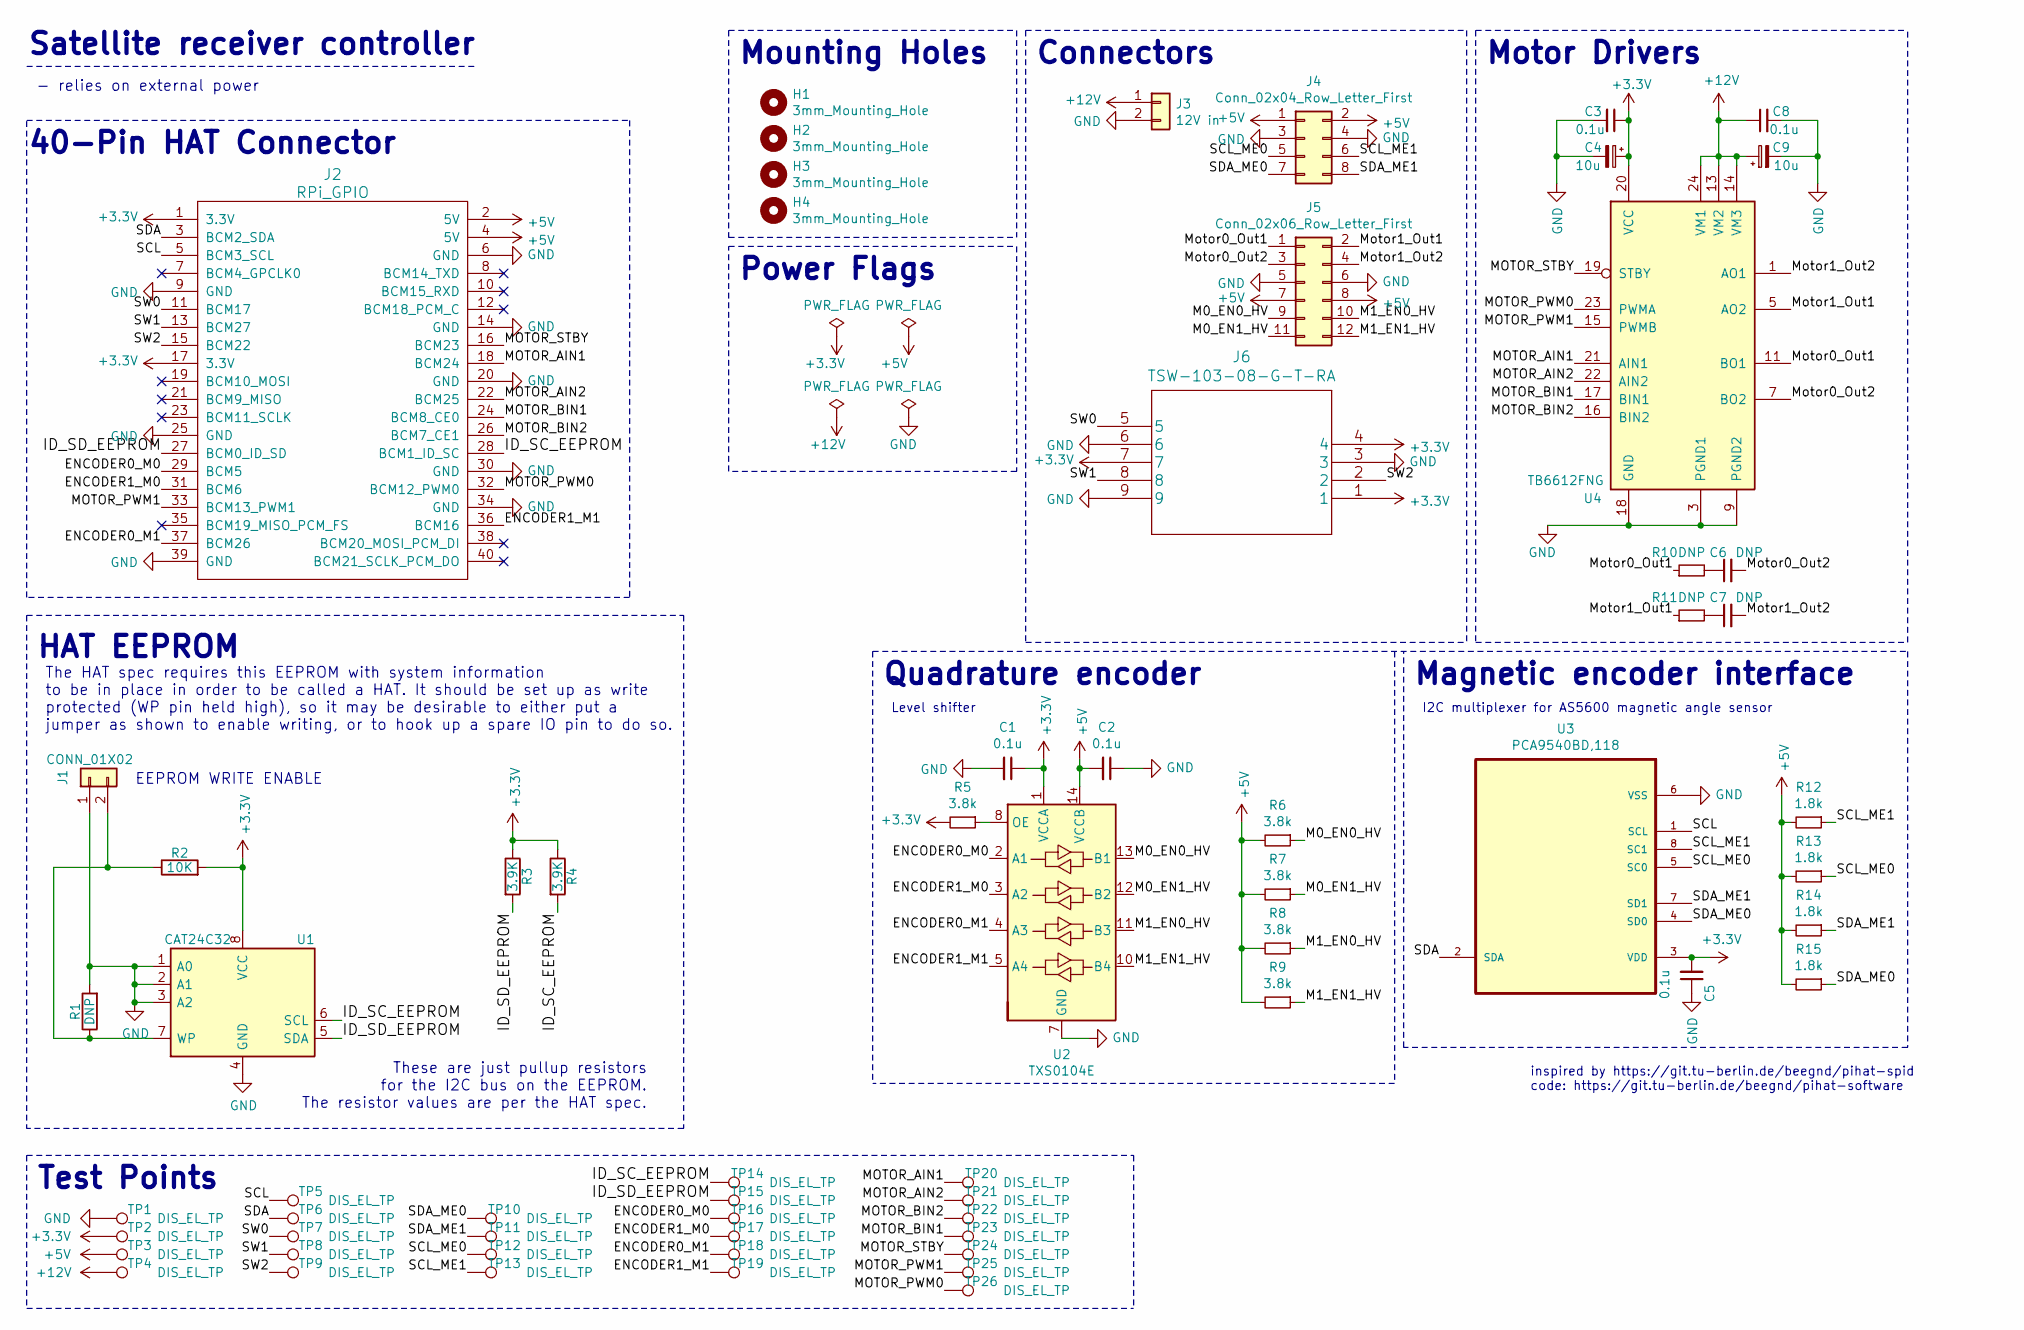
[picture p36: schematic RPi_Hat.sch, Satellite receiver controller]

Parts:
C1, C2, C3, C5, C8: 0.1u; C_0805_2012Metric_Pad1.18x1.45mm_HandSolder; Manufacturer_Part_Number 08055C104KAT2A; Digikey Part Number 478-1395-1-ND
C4, C9: 10u; C_0805_2012Metric_Pad1.18x1.45mm_HandSolder; Manufacturer_Part_Number CL21A106KOQNNNE; Digikey Part Number 1276-1096-2-ND
C6, C7: DNP; C_0805_2012Metric_Pad1.18x1.45mm_HandSolder
H1, H2, H3, H4: 3mm_Mounting_Hole; RPi_Hat_Mounting_Hole
J1: CONN_01X02; PinHeader_1x02_P2.54mm_Vertical; Manufacturer_Part_Number 77311-118-02LF; Digikey Part Number 609-4434-ND
J2: RPi_GPIO; PinSocket_2x20_P2.54mm_Vertical; Manufacturer_Part_Number 2222; Mouser Part Number 485-2222
J3: 12V in; PinHeader_1x02_P2.54mm_Horizontal; Manufacturer_Part_Number PH1RB-02-UA; Digikey Part Number 2057-PH1RB-02-UA-ND
J4: Conn_02x04_Row_Letter_First; PinHeader_2x04_P2.54mm_Horizontal; Manufacturer_Part_Number PH2RA-08-UA; Digikey Part Number 2057-PH2RA-08-UA-ND
J5: Conn_02x06_Row_Letter_First; PinHeader_2x06_P2.54mm_Horizontal; Manufacturer_Part_Number PH2RA-12-UA; Digikey Part Number 2057-PH2RA-12-UA-ND
J6: TSW-103-08-G-T-RA; Manufacturer_Part_Number TSW-103-08-G-T-RA; Digikey Part Number SAM8888-ND
R1, R10, R11: DNP; R_0805_2012Metric_Pad1.20x1.40mm_HandSolder
R2: 10K; R_0805_2012Metric_Pad1.20x1.40mm_HandSolder; Manufacturer_Part_Number CRCW080510K0FKEAC; Digikey Part Number 541-3976-1-ND
R3, R4: 3.9K; R_0805_2012Metric_Pad1.20x1.40mm_HandSolder; Manufacturer_Part_Number ERA-6AED392V; Digikey Part Number P123844CT-ND
R5, R6, R7, R8, R9: 3.8k; R_0805_2012Metric_Pad1.20x1.40mm_HandSolder; Manufacturer_Part_Number PAT0805E3791BST1; Digikey Part Number PAT3.79KBCT-ND
R12, R13, R14, R15: 1.8k; R_0805_2012Metric_Pad1.20x1.40mm_HandSolder; Manufacturer_Part_Number CRGCQ0805F1K8; Digikey Part Number A129752CT-ND
TP1, TP2, TP3, TP4, TP5, TP6, TP7, TP8, TP9, TP10, TP11, TP12, TP13, TP14, TP15, TP16, TP17, TP18, TP19, TP20, TP21, TP22, TP23, TP24, TP25, TP26: DIS_EL_TP; TestPoint_Pad_D1.0mm
U1: CAT24C32; SOIC-8_3.9x4.9mm_P1.27mm; Manufacturer_Part_Number CAT24C32WI-GT3; Digikey Part Number CAT24C32WI-GT3CT-ND
U2: TXS0104E; TSSOP-14_4.4x5mm_P0.65mm; Manufacturer_Part_Number TXB0104PWR; Mouser Part Number 595-TXS0104ED
U3: PCA9540BD,118; SOIC127P600X175-8N; Manufacturer_Part_Number PCA9540BD,118; Digikey Part Number 568-1844-1-ND
U4: TB6612FNG; SSOP-24_5.3x8.2mm_P0.65mm; Manufacturer_Part_Number TB6612FNG,C,8,EL; Digikey Part Number TB6612FNGC8ELCT-ND

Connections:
+3V3: C1.1, C3.1, C4.1, C5.2, J2.1 (3.3V), J2.17 (3.3V), J6.1, J6.4, J6.7, R2.2, R3.1, R4.1, R5.2, TP2.1, U1.8 (VCC), U2.1 (VCCA), U3.3 (VDD), U4.20 (VCC)
+5V: C2.2, J2.2 (5V), J2.4 (5V), J4.1, J4.2, J5.7, J5.8, R6.2, R7.2, R8.2, R9.2, R12.2, R13.2, R14.2, R15.2, TP3.1, U2.14 (VCCB)
+12V: C8.1, C9.1, J3.1, TP4.1, U4.13 (VM2), U4.14 (VM3), U4.24 (VM1)
/ENCODER0_M0: J2.29 (BCM5), TP16.1, U2.2 (A1)
/ENCODER0_M1: J2.37 (BCM26), TP18.1, U2.4 (A3)
/ENCODER1_M0: J2.31 (BCM6), TP17.1, U2.3 (A2)
/ENCODER1_M1: J2.36 (BCM16), TP19.1, U2.5 (A4)
/ID_SC_EEPROM: J2.28 (BCM1_ID_SC), R4.2, TP14.1, U1.6 (SCL)
/ID_SD_EEPROM: J2.27 (BCM0_ID_SD), R3.2, TP15.1, U1.5 (SDA)
/M0_EN0_HV: J5.9, R6.1, U2.13 (B1)
/M0_EN1_HV: J5.11, R7.1, U2.12 (B2)
/M1_EN0_HV: J5.10, R8.1, U2.11 (B3)
/M1_EN1_HV: J5.12, R9.1, U2.10 (B4)
/MOTOR_AIN1: J2.18 (BCM24), TP20.1, U4.21 (AIN1)
/MOTOR_AIN2: J2.22 (BCM25), TP21.1, U4.22 (AIN2)
/MOTOR_BIN1: J2.24 (BCM8_CE0), TP23.1, U4.17 (BIN1)
/MOTOR_BIN2: J2.26 (BCM7_CE1), TP22.1, U4.16 (BIN2)
/MOTOR_PWM0: J2.32 (BCM12_PWM0), TP26.1, U4.23 (PWMA)
/MOTOR_PWM1: J2.33 (BCM13_PWM1), TP25.1, U4.15 (PWMB)
/MOTOR_STBY: J2.16 (BCM23), TP24.1, U4.19 (STBY)
/Motor0_Out1: J5.1, R10.1, U4.11 (BO1), U4.12 (BO1)
/Motor0_Out2: C6.2, J5.3, U4.7 (BO2), U4.8 (BO2)
/Motor1_Out1: J5.2, R11.1, U4.5 (AO2), U4.6 (AO2)
/Motor1_Out2: C7.2, J5.4, U4.1 (AO1), U4.2 (AO1)
/SCL: J2.5 (BCM3_SCL), TP5.1, U3.1 (SCL)
/SCL_ME0: J4.5, R13.1, TP12.1, U3.5 (SC0)
/SCL_ME1: J4.6, R12.1, TP13.1, U3.8 (SC1)
/SDA: J2.3 (BCM2_SDA), TP6.1, U3.2 (SDA)
/SDA_ME0: J4.7, R15.1, TP10.1, U3.4 (SD0)
/SDA_ME1: J4.8, R14.1, TP11.1, U3.7 (SD1)
/SW0: J2.11 (BCM17), J6.5, TP7.1
/SW1: J2.13 (BCM27), J6.8, TP8.1
/SW2: J2.15 (BCM22), J6.2, TP9.1
GND: C1.2, C2.1, C3.2, C4.2, C5.1, C8.2, C9.2, J1.1, J2.6 (GND), J2.9 (GND), J2.14 (GND), J2.20 (GND), J2.25 (GND), J2.30 (GND), J2.34 (GND), J2.39 (GND), J3.2, J4.3, J4.4, J5.5, J5.6, J6.3, J6.6, J6.9, R1.2, TP1.1, U1.1 (A0), U1.2 (A1), U1.3 (A2), U1.4 (GND), U2.7 (GND), U3.6 (VSS), U4.3 (PGND1), U4.4 (PGND1), U4.9 (PGND2), U4.10 (PGND2), U4.18 (GND)
unnamed: C6.1, R10.2
unnamed: C7.1, R11.2
unnamed: J1.2, R1.1, R2.1, U1.7 (WP)
unnamed: R5.1, U2.8 (OE)

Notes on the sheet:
inspired by https://git.tu-berlin.de/beegnd/pihat-spid code: https://git.tu-berlin.de/beegnd/pihat-software
Motor Drivers
40-Pin HAT Connector
Connectors
Mounting Holes
Satellite receiver controller
- relies on external power
I2C multiplexer for AS5600 magnetic angle sensor
Quadrature encoder
Level shifter
Magnetic encoder interface
These are just pullup resistors for the I2C bus on the EEPROM. The resistor values are per the HAT spec.
The HAT spec requires this EEPROM with system information to be in place in order to be called a HAT. It should be set up as write protected (WP pin held high), so it may be desirable to either put a jumper as shown to enable writing, or to hook up a spare IO pin to do so.
HAT EEPROM
EEPROM WRITE ENABLE
Test Points
Power Flags

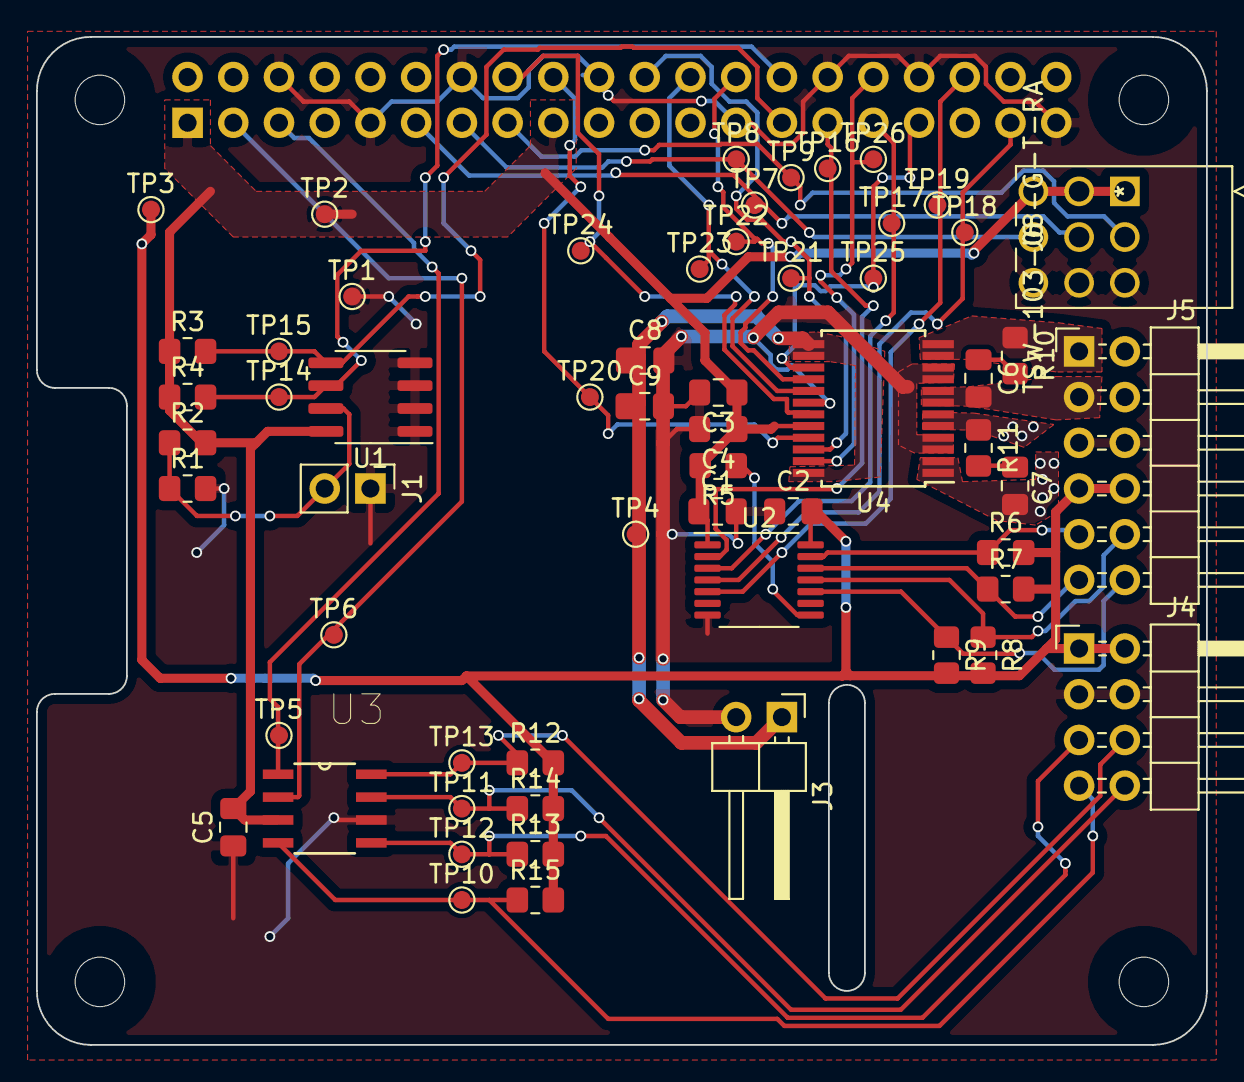
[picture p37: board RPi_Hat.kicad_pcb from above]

Board: 2 copper layers, 65.0 x 56.0 mm, 64 parts (1 on the bottom side), 38 nets.

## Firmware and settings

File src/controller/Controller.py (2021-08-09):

import time
import threading
import interface
from logzero import logger
from .SatelliteReceiver import SatelliteReceiver


class Controller(threading.Thread):
    """
    The Controller executes the instructions given by the Configuration.
    It also supervises the position and is responsible for the satellite receiver to not break itself.
    """
    def __init__(self, RC: interface.Configuration):
        super().__init__()
        self.sRec = SatelliteReceiver()
        self.RC = RC
        self._stop_event = threading.Event()

    def stop(self):
        self._stop_event.set()

    def run(self):
        """
        runs as a stoppable thread
        """
        while True:
            if self._stop_event.is_set():
                self.sRec.exit()
                return

            if self.RC.error:
                logger.info("error occurred")
                self.sRec.exit()
                return

            self.RC.actual_pos = self.sRec.get_rec_pos()

            if self.RC.state == interface.State.stop:
                self.sRec.stop()
            elif self.RC.state == interface.State.move_to_dir:
                speed = self.RC.speed
                self.sRec.move_dir(self.RC.desired_direction, speed)
            elif self.RC.state == interface.State.move_to_pos:
                self.sRec.move_pos(self.RC.desired_pos)

            time.sleep(0.1)

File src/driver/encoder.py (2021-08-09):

"""
Includes functionality to monitor the motors encoders
"""

import RPi.GPIO as GPIO
import Encoder
from enum import IntEnum


class EncoderPins(IntEnum):
    encoder0_m0 = 5
    encoder1_m0 = 6
    encoder0_m1 = 26
    encoder1_m1 = 16


def set_up_encoder() -> Encoder:
    """
    set up encoder GPIO
    :return: ready to use encoder object list
    """
    for pin in EncoderPins:
        GPIO.setup(pin, GPIO.OUT)
    encoder = [Encoder.Encoder(EncoderPins.encoder1_m1, EncoderPins.encoder0_m1),
               Encoder.Encoder(EncoderPins.encoder1_m0, EncoderPins.encoder0_m0)]
    return encoder

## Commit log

2021-05-24 set motor speed and direction
2021-05-24 add control for two motors
2021-05-24 readout motor encoder
2021-05-24 add simple PID
2021-05-24 add pid and direction controll
2021-05-27 use encoder direction and absolute position (demo included)
2021-06-07 include pi hat template
    [RPi_GPIO.sch, RPi_Hat.kicad_pcb, RPi_Hat.sch]
2021-06-07 simplify and adjust template
    [RPi_GPIO.sch, RPi_Hat.kicad_pcb, RPi_Hat.sch]
2021-06-11 add pi HAT schematic (spid hat as template)
    [RPi_Hat.sch]
2021-06-11 add rough pcb layout
    [RPi_Hat.kicad_pcb]
2021-06-21 finalize PCB layout
    [RPi_Hat.kicad_pcb, RPi_Hat.sch]
2021-06-21 adjust compontens, add BOM
    [RPi_Hat.sch, RPi_Hat.xlsx]
2021-07-15 include pcb features: i2c, magnetic encoder, hBridge subdivide code into driver and control logic update pins to pcb remove pid control example code: monitor motor rotation
2021-07-16 add switch driver
2021-07-24 include all rotctl functions separation in packages first angle translator
    [RPi_Hat.kicad_pcb, RPi_Hat.sch, RPi_Hat.xlsx]
2021-07-24 exit rotctl socket automatic, clean up, start rotator abstraction
2021-07-25 rename structure, move getAngle to shaft
2021-07-25 split position into receiver pos and shaft pos

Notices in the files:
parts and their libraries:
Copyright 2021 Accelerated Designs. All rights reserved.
